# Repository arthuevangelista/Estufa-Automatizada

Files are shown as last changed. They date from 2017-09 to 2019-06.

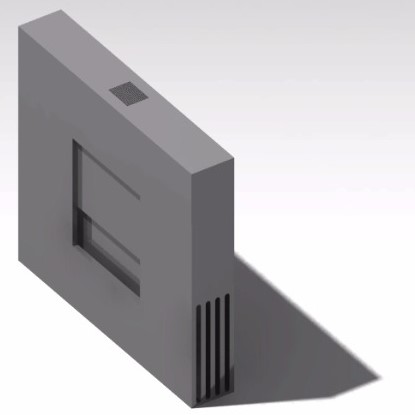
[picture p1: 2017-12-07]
Projeto Final/IMAGENS/WhatsApp Image 2017-11-26.jpeg

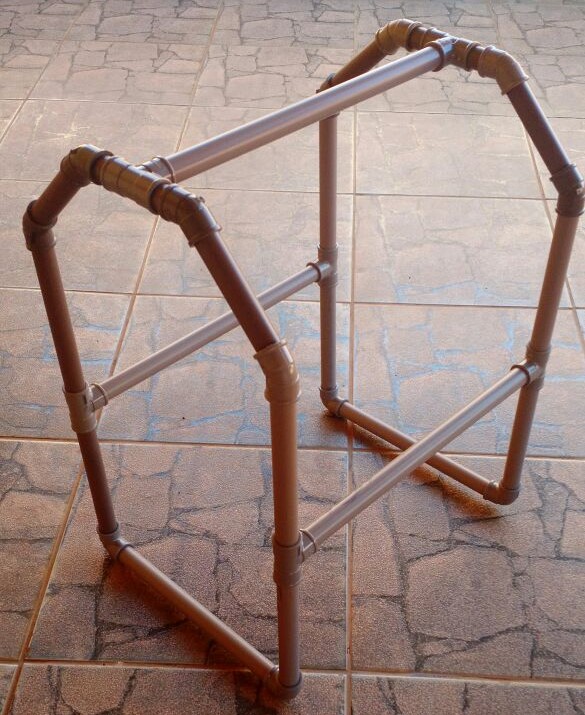
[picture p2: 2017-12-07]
Projeto Final/IMAGENS/WhatsApp Image 2017-11-24.jpeg

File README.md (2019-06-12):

# Estufa Automatizada

Este repositório possui um projeto de estufa automatizada para cultivo de morangos utilizando um microcontrolador MSP430. O projeto nasceu como relatório final da disciplina de Microprocessadores e Microcontroladores ministrada pelos professores Diogo Caetano (em 2017) e Gilmar Bezerra (em 2019) na UnB, campus Gama. As vantagens do uso do MSP430 são o seu baixo custo e seus modos de economia de energia. A proposta é fazer uma pequena cultivar de morangos que seja econômica e conceda as condições ideais de plantio. 

O repositório está organizado da seguinte forma:

- "Código" possui o código em C a ser compilado e carregado no MSP430. É recomendado o uso do software Code Composer Studio. Maiores instruções de instalação, compilação e carregamento podem ser encontradas nesta pasta. O módulo de interfaceamento do sensor DHT11 com o MSP430 foi disponibilizado pelo usuário [_bafeigum_](https://github.com/bafeigum/DHT11-Library-for-MSP430).  
- "Esquemático" possui todos os esquemáticos e diagramas de montagem do projeto. Neste diretório estão inclusos diagramas de PCI (placa de circuito impresso) caso sua produção seja optada. 
- "Relatório" possui alguns relatórios que os autores fizeram em relação ao projeto. Como este projeto nasceu de uma disciplina, esta pasta também possui o relatório final entregue ao professor. Não é recomendado o uso deste relatório por terceiros para fins acadêmicos por constituir plágio.  

Planos futuros para este projeto são a implementação de uma versão em Assembly e um aplicativo de celular ou _webapp_ para monitoramento e controle remoto das condições do plantio.

Autores: [Arthur Evangelista dos Santos](https://github.com/arthuevangelista) e [Guilherme Richard Alves de Oliveira](https://github.com/aogrichard).

O uso e distribuição deste projeto é livre, contanto que sejam identificados seus autores.

===========================================================================================

This repository contains a project of a automated stove for strawberry culture using a MSP430 microcontroller. This project started as a final report for the discipline of Microcontrollers and Microprocessors instructed by the professors Diogo Caetano (in 2017) and Gilmar Bezerra (in 2019) at UnB, Gama campus. The advantages of using the MSP430 are it's relative low cost and it's reduced energy consumption modes. The purpose is making a small strawberry culture that can be economic and provide the ideal plant conditions.

The repository is organized in the following way:

- "Código" has the code in C to be compiled and uploaded for the MSP430. It's recommended that you use Code Composer Studio. Further instructions of installation, compilation and code upload can be viewed in this folder as well. The module for interfacing the sensor DHT11 with MSP430 is provided by the user [_bafeigum_](https://github.com/bafeigum/DHT11-Library-for-MSP430).   
- "Esquemático" has all the schematics and diagrams for the project assembling. In this directory are included the PCB diagrams (printed circuit board) in case you choose to produce one.  
- "Relatório" has some reports that the autors have done in relation to the project. This folder has the final reports for the discline as this project started as a homework. It's not recommended to use those reports by third party with academic purposes as this could be considered plagiarism.  

Future plans for this project are it's implementation with a Assembly Language version and a smartphone app or _webapp_ for remote monitor and control of the plant conditions.

Authors: [Arthur Evangelista dos Santos](https://github.com/arthuevangelista) e [Guilherme Richard Alves de Oliveira](https://github.com/aogrichard).

The use and distribution of this project is free as long as it's authors are identified.

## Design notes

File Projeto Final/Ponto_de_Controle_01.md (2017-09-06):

Micro e Micro - 2.2017

# Ponto de Controle 01

## Projeto de Automação com MSP430

* **Justificativa**
    * O controle hídrico em lavouras, jardins residenciais e estufas tem papel fundamental nas finanças de uma empresa ou residência. Estima-se que boa parte dos gastos com água potável são devido a estas atividades. Em uma situação de crise hídrica como a atual e o preço da água se elevando a cada dia, uma empresa ou residência com controle de seus gastos hídricos obtém vantagem econômica expressiva.

* **Objetivos**
    * Economia de água devido a automação do ambiente;
    * Controle de irrigação do jardim/lavoura/plantação;
    * Captação de dados de umidade e temperatura ambiente;
    * Calcular e fornecer dados estatísticos como temperatura média, umidade relativa, desvios padrões e etc.
      
* **Requisitos**
    * Uso do launchpad MSP430;
    * Uso de uma memória flash externa para armazenamento do banco de dados;
    * Controle do fluxo de água com Relés e válvulas solenóides;
    * Sensores de umidade e temperatura;
    * Módulo Wi-Fi e Bluetooth;
    
* **Benefícios**
    * Uso da opção de low-power mode do MSP430 pode oferecer vantagem nos momentos em que não estiver sendo utilizado;
    * Relés e válvulas todas normalmente fechadas provê economia substancial de energia;
    * Controle hídrico
    
* **Revisão Bibliográfica**
    * 
    
* **Anotações Temporárias**

> Dúvida: Entrada de dados no sistema;

> Banco de dados ficaria armazenado em um dispositivo flash externo ao microcontrolador. Listas encadeadas podem ser uma boa abordagem para guardar elementos, adicionar/remover elementos e etc do banco de dados. **CUIDADO!** Listas são realizadas com alocação dinâmica de memória (pode dar problema na memória RAM do MSP430 se não for especificado que a lista deve estar na memo flash);

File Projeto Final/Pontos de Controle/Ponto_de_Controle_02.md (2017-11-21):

Micro e Micro - 2.2017

# Ponto de Controle 01

## Projeto de Automação com MSP430

* **Módulos utilizados no sistema**
	* Abaixo segue uma lista dos módulos que serão utilizados no sistema até a data de redação deste relatório
	
	* **Level-shifter para redução de tensão**
		* Uma montagem utilizando dois resistores de 10k ohm e um transistor mosfet BS170.
		* O level-shifter reduz a tensão para que seja possível conectar componentes que utilizam diferentes tensões como nível lógico alto. Se um sinal chega com 3,3 V o level-shifter subirá esta tensão para 5 V em sua saída para que seja utilizado por outro componente.
		* A recíproca é verdadeira. Portanto, se um sinal tiver 5 V, a saída do level-shifter terá 3,3 V.
		* Imagem do esquemático do componente abaixo.
		* Testes foram realizados com este componente para verificar se ele funciona e quais os níveis de tensão em sua saída. Houve também uma preocupação quanto à frequência máxima de operação, uma vez que este componente será utilizado na saída de todos os sensores e nas saídas do MSP430. Foi confirmada o nível de ruído apresentado na saída do level-shifter à partir de Hz, de acordo com a informação do datasheet do componente transistor BS170. As imagens abaixo mostram os resultados obtidos nos testes com osciloscópio.

> **LINK PARA DATASHEET DO BS170: https://www.onsemi.com/pub/Collateral/BS170-D.PDF**

   * **Módulo relé 4 canais**
       * Será utilizado um módulo com 4 relés para controle dos dispositivos com tensão de 12V e corrente
    * **Módulo sensor de umidade do solo (umidostato)**

		* Possui formato de garfo (apenas duas pontas que deverão estar fincadas no solo). Ao identificar umidade ocorrerá uma diferença de potencial entre as pontas do garfo. A corrente que passará entre as duas pontas é muito pequena (resistência próxima dos M ohm).

		* Quanto maior a resistência, menor a umidade entre as ponteiras. A corrente, portanto, é muito baixa para que se insira o sensor diretamente na porta analógica do micro. É necesário o uso de um módulo comparador.

			* Nada mais é que um amplificador operacional em modo comparador. Quando comprado o sensor, o comparador LM393 (low offset voltage dual comparator) vem no conjunto.

			* A tensão de trabalho é de 3,3 V a 5 V. O comparador tem quatro pinos: Vcc, GND, D0 (digital) e A0 (analógico). Para usar a saída digital é necessário utilizar o potenciômetro para calibrar o sensor.

			* O potenciômetro irá ajustar em qual medida de umidade a saída digital terá nível lógico zero. OBS.: Podemos utilizar uma entrada digital do MSP430 ativa em alta para identificar quando a umidade está baixa. Ou seja, Quando D0 = 1 -> Umidade baixa. Quando D0 = 0 -> Umidade no solo suficiente, desliga o irrigador.

			* Utilizaremos apenas o pino digital para o projeto. A leitura dos dados de umidade do solo podem ser comutados com a leitura dos dados de umidade do ar (DHT11), liberando a porta digital para outra aplicação.

			* Utilizar uma porta analógica para leitura de dados seria mais preciso, mas exigira um processamento do sinal analógico antes deste ser inserido no microcontrolador (i.e. uma média móvel dos valores para evitar ruído/sinal aleatório).

**REFERÊNCIAS**
> **LINK PARA SENSOR: https://www.filipeflop.com/produto/sensor-de-umidade-do-solo-higrometro/
	LINK PARA O DATASHEET DO LM393: http://www.ti.com/lit/ds/symlink/lm293.pdf**

	* Para visualização dos dados (umidade do ar, umidade do solo e temperatura) será utilizado um display. Dependendo da temperatura será ativado um exaustor (resfriar a estufa) ou uma lâmpada (aquecer a estufa); Da umidade do ar/solo serão ligadas as válvulas de irrigação.

		* Possui uma biblioteca na IDE do arduino #include<LiquidCrystal.h>
		* Pode ser facilmente implementada no MSP430
		* Utilizado para referência do usuário e para verificação dos dados da estufa

	* O sensor DHT11 é responsável por realizar a medição de umidade relativa do ar (usando um sensor do tipo HR202 (entre 20% e 90%)) e da temperatura (usando um termistor NTC (entre 0 e 50 C)). Possui quatro pinos: Vcc, GND, Dados (comunicação UART) e N.C (não utilizada)

		* Possui uma biblioteca própria no Arduino #include<dht.h>

		* Utiliza dois pinos para enviar os dados para o Microcontrolador (ambos analógicos). Para escrever os dados no display, é necessário separar os digitos.

		* É necessário um delay entre uma leitura e a outra (o micro enviará um sinal avisando que está em modo de leitura e o DHT11 enviará outro sinal indicando que está enviando dados). Será utilizada uma interrupção com o timer A para realizar a leitura dos dados.

		* Possui uma biblioteca para msp430 disponível no link do github a seguir: https://github.com/bafeigum/DHT11-Library-for-MSP430

		* Para utilizar esta biblioteca é necessário o uso de um timer e uma interrupção, uma vez que a leitura e escrita exigem um delay entre a comunicação com a placa.
			* Precisa estar setado em UP mode e contando a cada 250 kHz (pode-se utilizar o SMCLOCK sendo /4);
			* ISR seta um volatile unsigned char TOUT no TA0. Esse ISR também deverá dar clear na interrupt flag, setando CCIFG no registrador TACCL0;
			* São enviados 5 elementos de um vetor (chamado packet) para o MSP430:
				* packet[0] = primeiro byte de umidade
				* packet[1] = segundo byte de umidade (deve ser ZERO)
				* packet[2] = primeiro byte de temperatura
				* packet[3] = segundo byte de temperatura (deve ser ZERO)
				* packet[4] = byte da soma dos 4 bytes anteriores (usado para checagem dos dados (em caso de falha na comunicação))

**REFERÊNCIAS**
> **LINK PARA SENSOR: https://www.filipeflop.com/produto/sensor-de-umidade-e-temperatura-dht11/
	LINK PARA O DATASHEET DO DHT11: http://img.filipeflop.com/files/download/Datasheet_DHT11.pdf**

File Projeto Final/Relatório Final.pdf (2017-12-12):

# Estufa Agrícola Automatizada com Auxílio do MSP430 para Cultivo de Morangos

Arthur Evangelista dos Santos Universidade de Brasília, Faculdade do Gama — UnB, FGA Matrícula: 14/0016686
Email: arthuevangelista@hotmail.com

Gabriela Conceiçao dos Santos ˜ Universidade de Brasília, Faculdade do Gama — UnB, FGA Matrícula: 16/0152038
Email: gabrielacsantos.engunb@gmail.com

Abstract—Este projeto visa criar um prototipo de estufa ´ agrícola automatizada para o cultivo de morangos aplicando
sensores eletronicos para controlar as condiç ˆ | oes de umidade e ˜
temperatura com auxílio do microcontrolador MSP430.

Keywords—MSP430, microcontrolador, automaçao, morangos, ˜ estufa.

I. REVISAÕ BIBLIOGRAFICA ´
A. O Morangueiro

O morangueiro pertence a Família Rosaceae. De origem Europeia, as plantas cultivadas para o consumo de sua fruta ´ sao o resultado de um sucessivo trabalho de melhoramento ˜
genetico e cruzamento entre algumas esp ´ | ecies do G ´ | enero ˆ
Fragaria. Atualmente, existem mais de 15 variedades de morangueiros. E um vegetal rasteiro, de caule do tipo estolho, ´ produzindo gemas que permitem com que novas plantas, com raízes e folhas, sejam formadas, assexuadamente. Uma imagem do morangueiro encontra-se abaixo na Fig. 1. No Brasil, sua produçaõ e mais significativa nos meses de junho a dezembro ´
e requer boa umidificaçao do solo. Por este motivo, ˜ | acaros e ´
pulgoes s ˜ | ao suas principais pragas. ˜

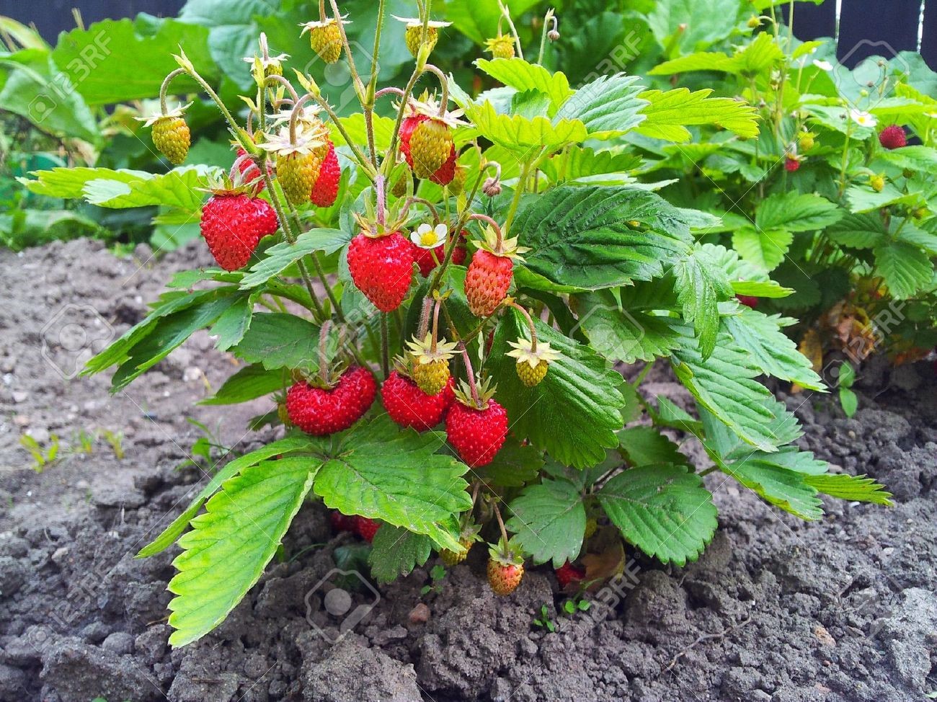
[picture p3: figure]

Fig. 1. Morangueiro

Desta planta origina-se o morango (Fig. 2), cuja parte
vermelha, comestível, e, na verdade, o recept ´ | aculo floral de- ´
senvolvido. Assim, ele e um pseudofruto; sendo os frutos, do ´ tipo aquenio, as estruturas amarronzadas que se encontram ˆ incrustadas nele.

Características gerais do cultivo do morango
:

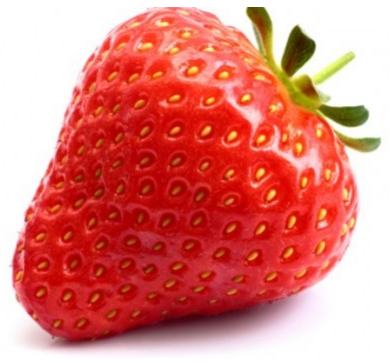
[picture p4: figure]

Fig. 2. Fruto e pseudofruto do morango

- Clima: Locais com temperatura alta durante o dia e baixa durante a noite sao considerados bons para o ˜ cultivo do morangueiro. O calor e importante para o ´ crescimento vegetativo das plantas, enquanto o frio é
imprescindível a frutificaçao. A floraç ˜ | | aõ e favorecida ´
por temperaturas abaixo de 10 ◦C e desfavorecida por temperaturas acima de 25 ◦C. O comprimento do
dia, ou seja, o numero de horas de luz, tamb ´ | | | em tem ´
influencia sobre a produç ˆ | ao. A estas caracter ˜ | ísticas é
dado o nome de fotoperíodo.
Fotoperíodo trata-se da proporçao entre luz e es- ˜ curidao num ciclo de 24 horas (Santos, D.M.M., ˜ 2004). O morango, classificado como planta C3
quanto a fotoss ` | íntese e short-day plant (SDP) quanto
ao fotoperíodo, deve estar exposto por volta de 8 a 10
horas de luz diaria. O per ´ | íodo de escuridao tamb ˜ | em´
possui influencia na produç ˆ | ao de flores. Por ˜ | em, o ´
pouco excesso de iluminaçao devido ˜ | as condiç ` | oes ˜
de solstício ou equinocio na regi ´ | ao n ˜ | ao ter ˜ | a tanta ´
influencia no desenvolvimento do vegetal. Por este
motivo, nao optou-se por um pl ˜ | astico preto ou de ´
coloraçao que evitasse a exposiç ˜ | aõ a iluminaç ` | | ao. ˜
Para manter o fotoperíodo em condiçoes ideias de ˜
plantio, sera utilizada uma interrupç ´ | ao no MSP430 que ˜
ativara um LED capaz de fornecer o espectro de luz ´ apropriado para a planta.
- Sistemas de cultivo: O morango pode ser cultivado em
canteiros a ceu aberto, em estufas e em combinaç ´ | aõ
com o uso de tunel baixo. Atualmente est ´ | | | a sendo ´
implantado o sistema de cultivo hidroponico. ˆ

- Local de plantio: O morangueiro produz melhor em solos areno-argilosos e bem drenados. As areas devem ´
ser de facil acesso e ter bom suprimento de ´ | agua ´
para irrigaçao. Deve ser evitado o plantio em local ˜ recentemente cultivado com tomate, batata, fumo ou
com o proprio morango. H ´ | a de se pesquisar sobre ´
outros metodos que tornem poss ´ | ível o plantio de
culturas morangos no mesmo local. Tambem deve ser ´ evitado o plantio em terras de baixa umida. ´
- Período de plantio: A epoca de plantio varia de acordo ´
com a regiao e a cultivaç ˜ | ao a ser plantada. De um ˜
modo geral, planta-se de janeiro a maio. Em regioes ˜
mais quentes, a epoca recomendada ´ | e de abril a ´
maio. Em locais com altitude acima de 1.000 metros, as cultivares de dia neutro podem ser plantadas até setembro.
- | Irrigaçao: A irrigaç ˜ | ao do morangueiro pode ser feita ˜
por aspersao, por ˜ | em o gotejamento (fertirrigaç ´ | ao) tem ˜
sido mais eficiente e economico. Por este motivo, ˆ
neste trabalho sera utilizado o m ´ | etodo de irrigaç ´ | aõ
por gotejamento. Geralmente irriga-se tres vezes por ˆ semana e com duraçao de 30 a 45 minutos, evitando ˜ o excesso de agua. ´
B. O Morangueiro no Distrito Federal

A cultura do morangueiro iniciou-se no Distrito Federal em meados da decada de 70, tendo sido primeiramente introduzida ´ e conduzida de forma empírica pelos agricultores de origem
japonesa vindos da regiao de Atibaia, S ˜ | ao Paulo, at ˜ | e hoje o ´
principal polo de produç ´ | ao de morango naquele estado. ˜

Estes agricultores pioneiros vieram iniciar o cultivo de hortaliças e de frutas para abastecer o novo mercado do Planalto Central. Muitos foram assentados pelo Instituto
Nacional de Colonizaçao e Reforma Agr ˜ | aria - INCRA, a partir ´
de 1970, no ”Projeto Integrado de Colonizaçao Alexandre ˜
Gusmao (PICAG)”, na Regi ˜ | ao Administrativa de Brazl ˜ | andia, ˆ
atualmente o principal produtor de morango do Distrito Federal.

A cultura do morango adaptou-se muito bem as condiçoes ˜ climaticas e de solo do Planalto Central, que apresenta altitude ´
de aproximadamente 1000 metros. Alem disso, essa regi ´ | aõ
possui temperaturas mais altas no verao, que favorecem a ˜
produçao de mudas e na sequ ˜ | encia passa por um inverno ˆ
ameno e seco, o que auxilia no período de floraçao, frutificaç ˜ | aõ
e melhora de forma significativa a qualidade dos frutos cultivados.
Segundo a Emater-DF (Empresa de Assistencia T ˆ | ecnica ´
e Extensao Rural do Distrito Federal), no ano de 2016, a ˜ safra de morangos no Distrito Federal alcançou cerca de 5250 toneladas, numeros que colocam o Distrito Federal na disputa ´ do sexto lugar da produçao nacional entre os estados produ- ˜
tores da fruta . Sao, em m ˜ | edia, 240 produtores de morango ´
em todo o DF. Desses, 35% de produtores agrícolas da cidade sao os que distribuem o que se consome no DF. ˜
C. Estufas Agrícolas

Em grande parte da historia da humanidade, fomos ´ caçadores-coletores. Ha cerca de 10.000 anos, começamos a ´ domesticar plantas e animais como uma forma de tornar a nossa oferta de alimentos mais acessível e previsível.

Sendo assim, para melhorar a produçao agr ˜ ícola, surgiram as estufas agrícolas. O objetivo do cultivo agrícola em estufas
e proporcionar um ambiente controlado, em relaç ´ | ao a fatores ˜
climaticos como temperatura, umidade, luz e quantidade de ´ agua (rega), para que as plantas possam ter um crescimento ´ em um ambiente ideal (Silva, 1976).

A estrutura de uma estufa agrícola depende bastante de
sua finalidade. Geralmente, e constitu ´ | ída por uma armaçao, ˜
de alumínio ou outro material resistente, com uma altura suficiente para poder cultivar e caminhar dentro sem incomodos, ˆ
ela e coberta por um pl ´ | astico transparente, em alguns casos ´
possui uma tela, conhecida como sombrite, que auxilia na regulagem da temperatura interna da estufa alem de ventiladores ´ e em alguns casos lampadas para o controle de luminosidade ˆ (Fig. 3).

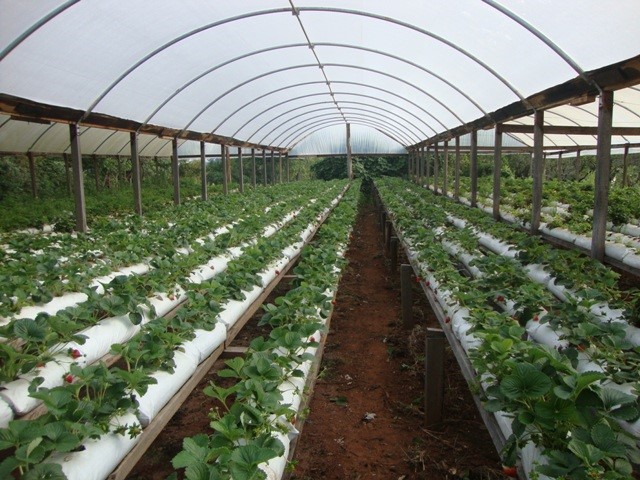
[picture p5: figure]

Fig. 3. Estrutura de uma estufa convencional para o cultivo de morangos

O aumento significativo da utilizaçao de estufas se deu, ˜
em parte, pela criaçao do pl ˜ | astico, devido ao seu baixo custo e ´
versatilidade, porem existem outros fatores que influenciam tal ´ fato, como o melhor desenvolvimento do plantio, aumento de produtividade, colheita nas entressafras e produtos de melhor qualidade.
D. Automaçao de Estufas ˜

Em uma estufa existem diversas variaveis que podem ser ´ monitoradas e verificadas para o controle do plantio, como temperatura, umidade e luminosidade. Considerando o ponto de vista dos produtores agrícolas, a correta leitura dos dados e posterior tomada de decisao pode trazer resultados satis- ˜ fatorios. ´

A automatizaço de uma estufa ˜ | e uma excelente ferramenta ´
de auxílio ao agricultor, pois permite a tomada de deciso no ˜
momento certo, conforme a analise das vari ´ | aveis verificadas. ´

II. JUSTIFICATIVA

Apesar de ser considerado um dos maiores produtores de morango do Brasil, durante o de 2017, o Distrito Federal veio enfrentando um grave crise hídrica, o que afetou de

forma significativa a produçao de morangos nessa regi ˜ | ao. ˜
Segundo dados da Emater, a restriçao no abastecimento de ˜
agua provocou a diminuiç ´ | ao da ˜ | area plantada em cerca de ´
30%, de 150 hectares em 2016 para 105 hectares neste ano.
Alem disso, a desaceleraç ´ | ao na produç ˜ | ao de mercado de ˜
morangos do DF ocasionou a diminuiçao do n ˜ | umero de tra- ´
balhadores envolvidos direta e indiretamente com a atividade, gerando a queda na renda das famílias e do Produto Interno Bruto(PIB) do Morango.

Diante disso, a escolha do projeto de construçao de uma ˜ estufa automatizada foi motivada pela simples possibilidade de se oferecer uma nova alternativa para o melhoramento do cultivo de morangos no Distrito Federal , uma vez que a estufa proposta sera capaz de controlar todas as necessi- ´ dades da cultura e o ambiente da estufa, o que proporcionará aos produtores mais qualidade em seus frutos e uma maior
renda. Tambem ser ´ | a poss ´ | ível controlar a quantidade de agua ´
utilizada na irrigaçao da plantaç ˜ | ao gerando, consequentemente, ˜
economia de recursos hídricos e financeiros na produçao de ˜ morangos.

III. OBJETIVOS

Considerando que cada especie de planta necessita de ´
situaçoes clim ˜ | aticas diferentes e espec ´ | íficas para se desen-
volver, o projeto proposto tem o intuito de otimizar o cultivo de morangos atraves do desenvolvimento de uma estufa capaz de ´ gerenciar (monitorar e atuar) o controle das condiçoes ambien- ˜
tais dentro do ambiente da estufa atraves da disponibilizaç ´ | aõ
de recursos de automaçao como irrigaç ˜ | ao autom ˜ | atica, sistemas ´
de ventilaçao, iluminaç ˜ | ao e controle de temperatura ambiente, ˜
utilizando o microcontrolador MSP430.

Em resumo, os objetivos deste trabalho sao: ˜

- | Economia de agua devido a automaç ´ | ao do ambiente; ˜
- Captaçao de dados de umidade e temperatura ambi- ˜ ente;
- Captaçao de dados de umidade do solo; ˜
- Controle de irrigaçao da estufa; ˜
- | Controle da iluminaçao e do fotoper ˜ | íodo da planta;
- Controle da temperatura no ambiente interno da estufa;
- Apresentaçao dos dados adquiridos pelos sensores ao ˜ usuario. ´

IV. REQUISITOS
- Uso do launchpad MSP430;
- | Controle do fluxo de agua com Rel ´ | es e v ´ | alvulas ´
| solenoides; ´
- Sensores de umidade e temperatura;
- Display para apresentaçao dos dados; ˜
- Fontes para fornecimento de 3.3 V, 5 V e 12 V para
| o sistema;
- LED capaz de fornecer o espectro de luz necessario ´
| para planta;
- | Pastilha termica para o r ´ | apido ajuste de temperatura; ´
V. BENEFÍCIOS
- | Uso da opçaõ | low-power mode do MSP430 pode
oferecer vantagem nos momentos em que nao estiver ˜ sendo utilizado;
- | Os reles e v ´ | alvulas todas e modo normalmente fechado ´
(NC) prove economia substancial de energia; ˆ
- Controle do consumo de recursos hídricos;
- Monitoramento do crescimento da planta e dos relacionados ao microclima no qual ela se encontra;
- Certeza de colheita no período de safra e entressafra;
- Economia de tempo e dinheiro para o produtor com o trabalho relacionado ao plantio e colheita dos morangos.

VI. ESTRUTURA

A estrutura do prototipo da estufa foi inicialmente cons- ´ truída com canos PVC (Policloreto de Vinila) de 25 mm de
diametro, e coberta com filme pl ˆ | astico transparente. A escolha ´
desses materiais foi feita pois se tratam de materiais resistentes, acessíveis, de baixo custo e suprem bem as necessidades de controle do mini-ecossistema da estufa. Como mencionado
tambem na seç ´ | ao I-A, n ˜ | ao optou-se por um pl ˜ | astico preto ou ´
de coloraçao que evitasse a exposiç ˜ | aõ a iluminaç ` | ao. ˜

As dimensoes da estruturas foram determinadas a partir da ˜ densidade de plantio estipulada para o cultivo do morangueiro em estufas, onde esta define que o espaçamento entre os morangueiros deve ser de no mínimo 20 cm e altura maxima ´ que a planta pode atingir 30 cm.

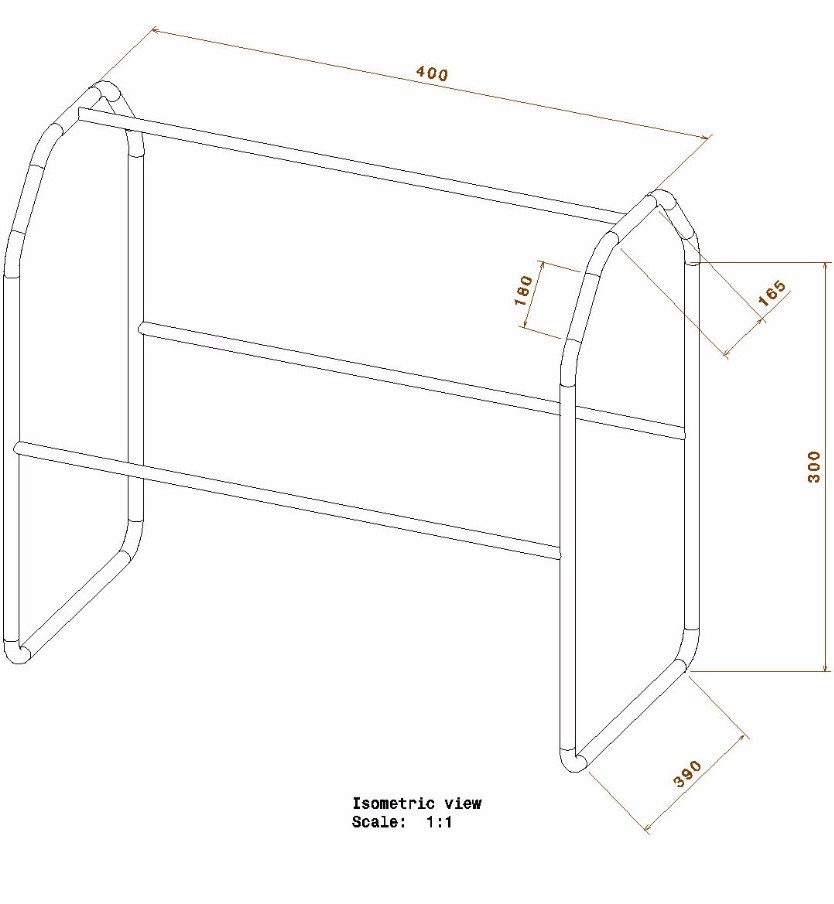
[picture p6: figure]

Fig. 4. Vista Isometrica do CAD da Estrutura realizado no software CATIA. ´


Fig. 5. Estrutura construída em cano PVC.

VII. COMPARTIMENTO PARA ELETRONICA ˆ

Tendo em vista a acomodaçao dos componentes ˜ eletronicos, optou-se por montar uma segunda estrutura ˆ para concentrar tais componentes. Trata-se de uma caixa de
madeira MDF onde serao concentrados: o MSP430, o m ˜ | odulo ´
level-shifter, o display de cristal líquido, a pastilha termica e ´
os coolers, as fontes de alimentaçao e o m ˜ | odulo rel ´ | e. Assim, ´
a realizaçao da manutenç ˜ | ao em algum destes componentes ˜
torna-se de facil acesso. Outra vantagem ´ | e a facilidade de ´
acesso quanto a etapa de testes nos componentes e validaçaõ de algoritmos no MSP430. Os demais componentes (os sensores DHT11, umidostato e o LED de espectro completo) devem interagir diretamente com o ambiente interno a estufa `
e, portanto, estao no interior do pl ˜ | astico transparente de ´
cobertura da estufa.
Esta caixa contara com aberturas para circulaç ´ | ao de ar na ˜
regiao inferior e na superior, como pode ser observado nas ˜ Fig. 6 e no detalhamento na Fig. 7. A motivaçao para esta ˜
configuraçao se d ˜ | a pela exaust ´ | ao do cooler de resfriamento ˜
da pastilha termica estar contida neste compartimento. A ´ configuraçao das aberturas inferiores favorece o estrangula- ˜ mento do fluxo de ar, aumentando sua velocidade e fazendo com que o ar frio e menos denso resfrie os componentes do compartimento interno. As aberturas superiores tambem´ estrangulam o fluxo de ar, fazendo com que o ar quente e interno do compartimento saia com maior velocidade para o ambiente externo.
Maiores detalhes quanto a configuraç ` | ao dos coolers e ˜
o funcionamento da pastilha termica estar ´ | ao na seç ˜ | ao VIII. ˜
Resumidamente, a pastilha e um paralelep ´ | ípedo com pouca
espessura. Esta aquecera de um lado e resfriar ´ | a do outro ´
e as aletas de alumínio em conjunto com os coolers seraõ responsaveis pela troca de calor externo. Como ambos os lados ´ poderao aquecer ou resfriar, foram colocadas aletas e coolers ˜ nos dois lados. Este conjunto esta apoiado no compartimento ´
para eletronica e um dos lados estar ˆ | a virado para o interior da ´
estufa.

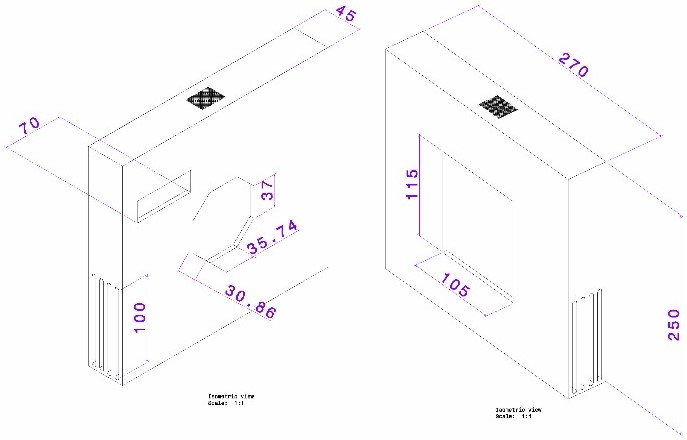
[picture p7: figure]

Fig. 6. Vista Isometrica do CAD do compartimento para eletr ´ | onica realizado ˆ
no software CATIA.

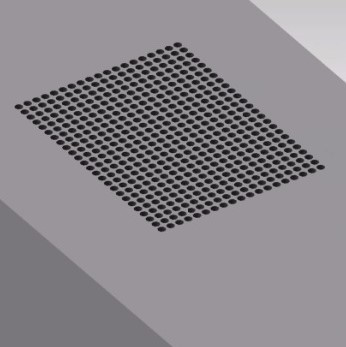
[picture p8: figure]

Fig. 7. Detalhamento da abertura superior do compartimento para eletronica. ˆ

VIII. VISAÕ GERAL DO SISTEMA

O sistema do projeto proposto pode ser dividido duas partes. Uma parte de hardware, dotado do microcontrolador
MSP430, sensores eletronicos, os quais s ˆ | ao encarregados pela ˜
aquisiçao de dados do sistema, e atuadores, respons ˜ | aveis por ´
irrigar, iluminar, ventilar e reduzir ou aumentar a temperatura. E uma parte de software, responsavel pelo processamento dos ´ dados e do controle dos perifericos atuadores. ´

A. Hardware
1) Lista de Componentes:
- MSP-EXP430G2553LP;
- Sensor de luz (LDR 5mm);
- Sensor de temperatura e umidade (DHT11);
- Resistores de 10kOhm;
- Transistor Mosfet BS170;
- Modulo sensor de umidade do solo (Umidostato); ´
- | Modulo rel ´ | e 4 canais; ´
- LED de espectro completo;
- Pastilha termina de efeito Peltier TEC1-12706; ´
- 2 Coolers de 12V;
- Fontes de 3,3V, 5V e 12V;
- | Valvula Solen ´ | oide. ´
2) Descriçao do Hardware: ˜ | Para melhor ilustrar a mon-
tagem dos componentes, foi realizado um diagrama de blocos para o sistema, que pode ser visualizado na Fig. 8. Uma breve
descriçao de cada componente ser ˜ | a apresentada a seguir. ´

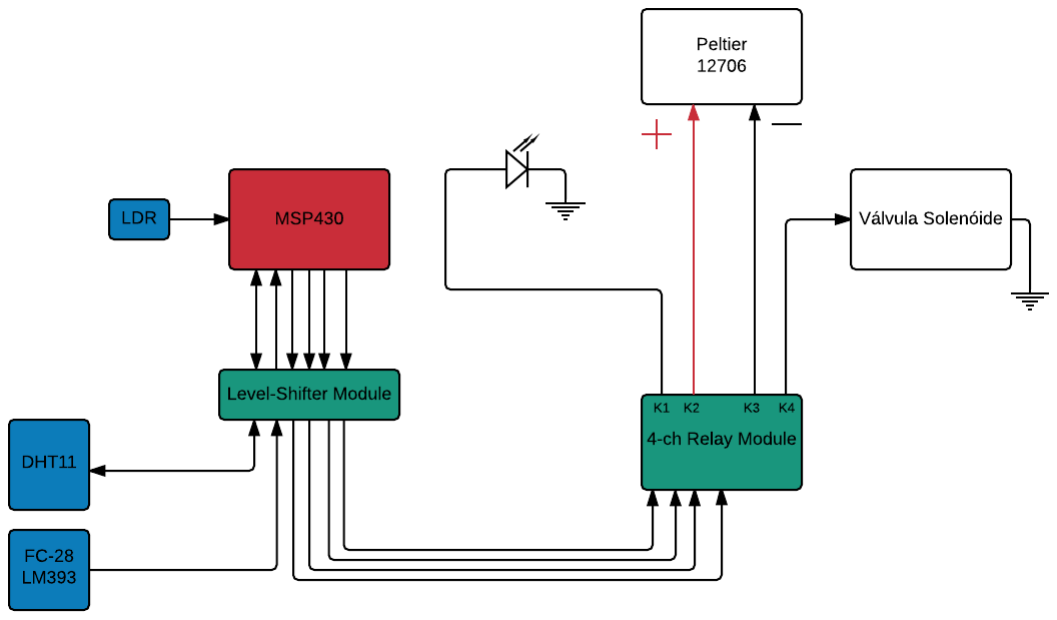
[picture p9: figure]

Fig. 8. Diagrama de Blocos do sistema da estufa.

- MSP-EXP430G2553LP: O MSP430 sera o micro- ´ controlador responsavel pelo processamento dos dados ´ e a tomada de decisao de acordo com os dados. ˜ Este componente recebera os dados de temperatura e ´ umidade relativa do ar no interior da estufa, os dados de umidade do solo e os dados de luminosidade e
tomara as decis ´ | oes melhor descritas na seç ˜ | ao VIII-A3. ˜
- Sensor de luz (LDR 5mm): Apos consultoria a ´
colegas da area de fisiologia vegetal e devido ´ | as`
características fotoperiodicas do morango, foi optado ´ pelo uso de um sensor de luminosidade LDR (Light Dependent Resistor) para identificar a existencia ou ˆ
nao de luminosidade na regi ˜ | ao pr ˜ | oxima ´ | a planta. O `
sensor e basicamente um resistor que ao submetido ´ | à
luz, aumenta sua condutividade eletrica. ´
- | Level-shifter para reduçao de tens ˜ | ao: ˜ | Uma mon-
tagem utilizando dois resistores de 10k ohm e um transistor mosfet BS170. O level-shifter reduz a tensaõ para que seja possível conectar componentes que
utilizam diferentes tensoes como n ˜ | ível logico alto. Se ´
um sinal chega com 3,3 V o level-shifter subira esta ´
tensao para 5 V em sua sa ˜ | ída para que seja utilizado
por outro componente.
A recíproca e verdadeira. Portanto, se um sinal tiver ´ 5 V, a saída do level-shifter tera 3,3 V. Testes foram ´ realizados com este componente para verificar se ele
funciona e quais os níveis de tensao em sua sa ˜ | ída.
Houve tambem uma preocupaç ´ | ao quanto a frequ ˜ | encia ˆ
maxima de operaç ´ | ao, uma vez que este componente ˜
sera utilizado na sa ´ | ída de todos os sensores e nas
saídas do MSP430. Foi confirmada o nível de ruído apresentado na saída do level-shifter a partir de 5MHz, o que ratifica a informaçao fornecida pelo ˜ datasheet do componente transistor BS170.
O esquematico desta montagem encontra-se na Fig. 9 ´ abaixo.

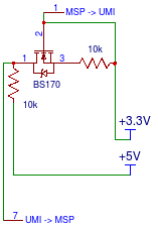
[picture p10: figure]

Fig. 9. Esquematico da unidade ´ | level-shifter (redutora de tensao). ˜
Tambem foi realizada um esquem ´ | atico para todos ´
redutores de tensao que ser ˜ | ao utilizados no projeto e ˜
foi montada um layout para placa de circuito impresso (PCB do inglesˆ printed circuit board). O intuito de se utilizar uma PCB e facilitar a montagem do circuito e ´
evitar perdas de tensao, diminuindo o ru ˜ | ído devido as`
linhas de transmissao do sinal. At ˜ | e a data de redaç ´ | aõ
deste relatorio, a PCB encontra-se em sua vers ´ | ao 1.0. ˜
O estudo quanto ao uso de ground plate para reduçaõ
de ruído esta em andamento para as demais vers ´ | oes. ˜
- | Modulo rel ´ | e 4 canais: ´ | Sera utilizado um m ´ | odulo ´
com 4 reles para controle dos dispositivos com tens ´ | aõ
de 12V (pastilha termica e a v ´ | avula solen ´ | oide) e do ´
LED de espectro completo de 3,3V que consume uma corrente acima da suportada pelo MSP430

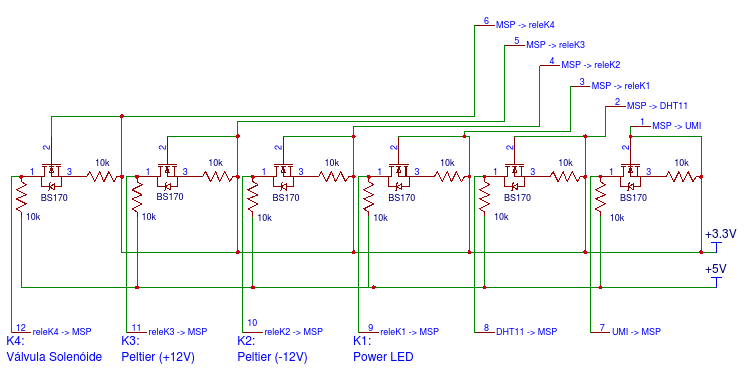
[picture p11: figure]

Fig. 10. Esquematico do bloco de ´ | level-shifter’s utilizados no projeto.

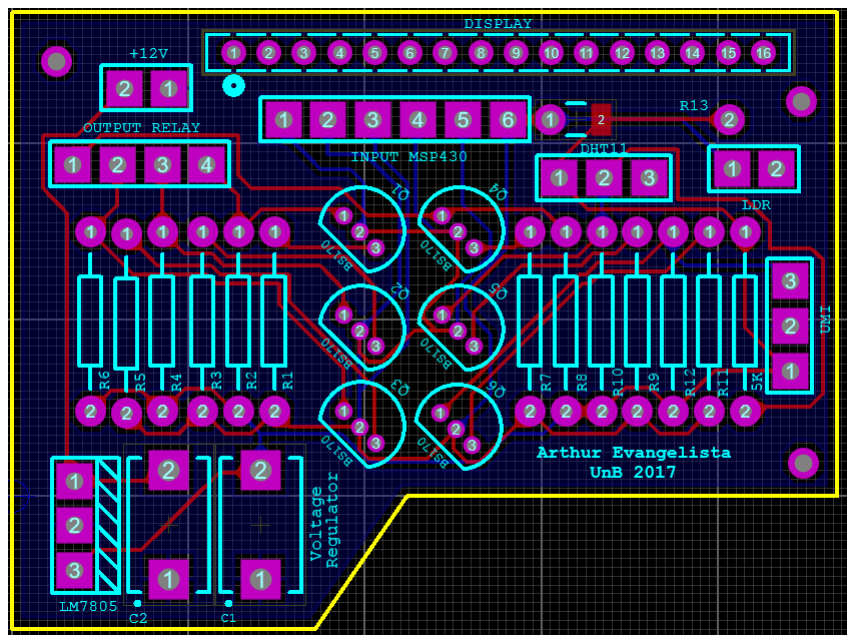
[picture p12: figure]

Fig. 11. Layout para PCB a ser confeccionada para o projeto.

- Modulo sensor de umidade do solo (umidostato): ´ Possui formato de garfo (apenas duas pontas que deverao estar fincadas no solo). Ao identificar umidade ˜ ocorrera uma diferença de potencial entre as pontas do ´
garfo. A corrente que passara entre as duas pontas ´ | é
muito pequena (resistencia pr ˆ | oxima dos M ohm). ´
Quanto maior a resistencia, menor a umidade entre as ˆ ponteiras. A corrente, portanto, e muito baixa para que ´ se insira o sensor diretamente na porta analogica do ´
micro. E necess ´ | ario o uso de um m ´ | odulo comparador. ´
Nada mais e que um amplificador operacional em ´ modo comparador. Quando comprado o sensor, o comparador LM393 (low offset voltage dual comparator) vem no conjunto.
A tensao de trabalho ˜ | e de 3,3 V a 5 V. O comparador ´
tem quatro pinos: Vcc, GND, D0 (digital) e A0
(analogico). Para usar a sa ´ | ída digital foi necessario ´
utilizar o potenciometro j ˆ | a encontrado no m ´ | odulo para ´
calibrar o sensor.
O potenciometro ir ˆ | a ajustar em qual medida de umi- ´
dade a saída digital tera n ´ ível logico zero. Podemos ´ utilizar uma entrada digital do MSP430 ativa em alta para identificar quando a umidade esta baixa. Ou seja, ´ Quando D0 = 1 a umidade esta baixa. Quando D0 = ´
0, ha umidade suficiente, n ´ | ao h ˜ | a necessidade de ligar ´
o irrigador (valvula solen ´ | oide). ´
Utilizaremos apenas o pino digital para o projeto. A leitura dos dados de umidade do solo podem ser comutados com a leitura dos dados de umidade do ar (DHT11), liberando a porta digital para outra aplicaçao. ˜
Utilizar uma porta analogica para leitura de dados ´ seria mais preciso, mas exigira um processamento do ´ sinal analogico antes deste ser inserido no microcon- ´ trolador (tecnicas de amostragem do sinal, uso do ´
criterio de Nyquist e o uso de uma m ´ | edia m ´ | ovel ou ´
filtro digital para evitar ruído ou sinais aleatorios ´ | ).
- Display de Cristal Líquido: Para visualizaço dos ˜ dados (umidade do ar, umidade do solo e temperatura) sera utilizado um display. Dependendo da temperatura ´ sera ativado um exaustor (ventilar a estufa) e uma ´ pastilha termica (aquece ou resfria o ambiente da est- ´
ufa). Da umidade do ar/solo serao ligadas as v ˜ | alvulas ´
de irrigaçao. ˜
Possui uma biblioteca na IDE do arduino: (#include¡LiquidCrystal.h¿) e pode ser facilmente implementada no MSP430 utilizando algoritmos disponíveis na documentaçao do fabricante. O display ˜
sera meramente utilizado para refer ´ | encia do usu ˆ | ario ´
quanto aos dados do mini-clima da estufa.
- | Sensor DHT11: O sensor DHT11 e respons ´ | avel por ´
realizar a mediçao de umidade relativa do ar (usando ˜ um sensor do tipo HR202 (entre 20% e 90%)) e da temperatura (usando um termistor NTC (entre 0 e 50 ◦C)). Possui quatro pinos: Vcc, GND, Dados (comunicaçao UART) e N.C (pino vazio). Possui uma ˜ biblioteca propria no Arduino #include¡dht.h¿. ´
Para escrever os dados no display, e necess ´ | ario separar ´
os dígitos. Por se tratar de um sensor de comunicaçaõ
UART, e necess ´ | ario um delay entre uma leitura e a ´
outra. O MSP430 enviara um sinal para o ´ | slave (o
sensor) avisando que esta em modo de leitura e o ´
DHT11 enviara outro sinal para o ´ | master (o MSP430)
indicando que esta enviando dados. Ser ´ | a utilizada uma ´
interrupçao com o timer A para realizar o delay de ˜ leitura dos dados.
Possui uma biblioteca para MSP430 disponível no link do github a seguir: https://github.com/bafeigum/DHT11-Library-for-MSP430.
O princípio de funcionamento desta biblioteca é semelhante ao descrito anteriormente. E utilizado um ´
timer (o timer A) e uma interrupçao para comunicaç ˜ | aõ
com a placa:
- Precisa estar setado em UP mode e contando a cada 250 kHz (pode-se utilizar o SMCLOCK sendo /4);
- ISR seta um volatile unsigned char TOUT no
TA0. Esse ISR tambem dever ´ | a dar clear na ´
interrupt flag, setando CCIFG no registrador TACCL0;
- Sao enviados 5 elementos de um vetor ˜ (chamado packet) para o MSP430: packet[0] = primeiro byte de umidade packet[1] = segundo byte de umidade (deve ser ZERO)
packet[2] = primeiro byte de temperatura packet[3] = segundo byte de temperatura (deve ser ZERO)

packet[4] = byte da soma dos 4 bytes anteriores (usado para checagem dos dados (em caso de falha na comunicaçao)) ˜

- | Valvula Solen ´ | oide: ´ | Basicamente uma chave de
| pressao. Quando passa corrente pelos seus terminais ˜
ele libera a passagem do fluxo de agua. Caso contr ´ | ario, ´
a valvula se mant ´ | em em estado normalmente fechado ´
| e nao consome energia. ˜
- LED de Espectro Completo: O LED de espectro completo utilizado pode ser visualizado na Fig. 12 abaixo. Este LED utiliza uma alimentaçao de 3,3V ˜ e consome por volta de 0,9 A de corrente, fornecendo quase 3W de potencia luminosa para o sistema. De ˆ
acordo com o grafico da Fig. 13, dispon ´ | ível no
datasheet do componente, o espectro de luz que este
| LED fornece e o suficiente para manter a fotoss ´ | | íntese
da planta no trecho de claridade de seu fotoperíodo. Para controlar este LED, sera utilizado o canal K1 do ´
| rele, ligado a uma das sa ´ | | ídas do MSP430. A escolha
para esta configuraçao se deve ˜ | a corrente consumida `
pelo LED que e muito superior ´ | a maior corrente `
fornecida pelo MSP430. Outra vantagem de se utilizar
| o modulo rel ´ | é e a proteç ´ | ao contra fugas de corrente ˜
| do rele para o dispositivo que o controla. ´

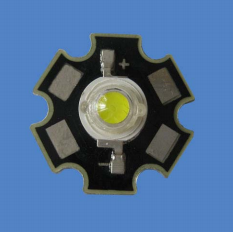
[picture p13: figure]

Fig. 12. LED de espectro completo e da PCB de alumínio do conjunto.

- Pastilha Termica de Efeito Peltier TEC1-12706: ´
Sera utilizada uma pastilha t ´ | ermica de efeito Peltier ´
(TEC1-12706) em conjunto com os Coolers de 12V para o aquecimento e resfriamento da estufa. Esta pastilha necessita de uma fonte de alimentaçao de ˜ 12V e consome ate 6A para manter o efeito em ´ sua superfície. O efeito Peltier ocorre quando dois materiais, quando aplicada uma corrente, em uma junçao do material dissipar calor e na outra absorver ˜ calor. A energia dissipada ou absorvida e proporcional ´ a corrente eletrica (Bobean, 2013). ´
A pastilha TEC1-12706 (Fig. 14) utilizada neste pro-
jeto prove resfriamento de at ˆ | e -30 ´

◦C de uma lado
e aquecimento de ate +70 ´ | ◦C do outro. Para evitar a
queima do componente, transferir o calor do ambiente para a pastilha e vice-versa, e aumentar a area de fluxo ´

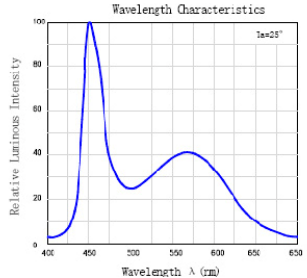
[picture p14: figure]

Fig. 13. Grafico da caracter ´ | ística optica do LED de espectro completo ( ´ | fonte:
3W High Power LED datasheet).
termico, foram instaladas aletas de alum ´ | | ínio. As aletas
transferem o calor do e para o ambiente pelo fenomeno ˆ de conduçao t ˜ ermica. ´

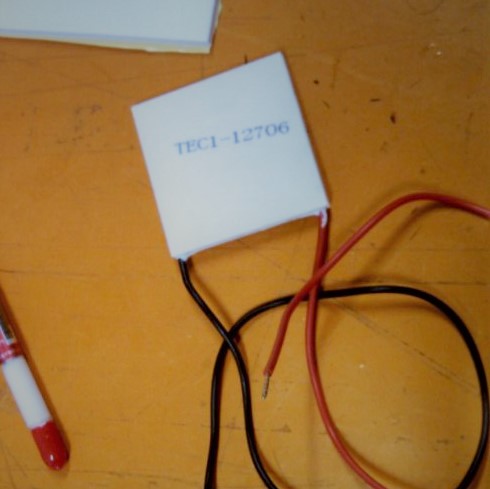
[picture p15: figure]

Fig. 14. Pastilha Termica de Efeito Peltier TEC1-12706. ´

Como citado brevemente na seçao VII, ambos os ˜ lados da pastilha poderao aquecer ou resfriar, a de- ˜ pender da polaridade da tensao submetida. Portanto, ˜ foram colocadas aletas e coolers nos dois lados da pastilha. O conjunto esta apoiado no compartimento ´
para eletronica e um dos lados estar ˆ | a virado para o ´
interior da estufa.
Testes foram realizados com o conjunto montado para certificar seu funcionamento. Quando invertida a polaridade da tensao pelos canais K2 e K3 do ˜

modulo rel ´ | e, a pastilha rapidamente aquece ou resfria. ´
A Fig. 15 a seguir melhor ilustra o funcionamento deste conjunto.

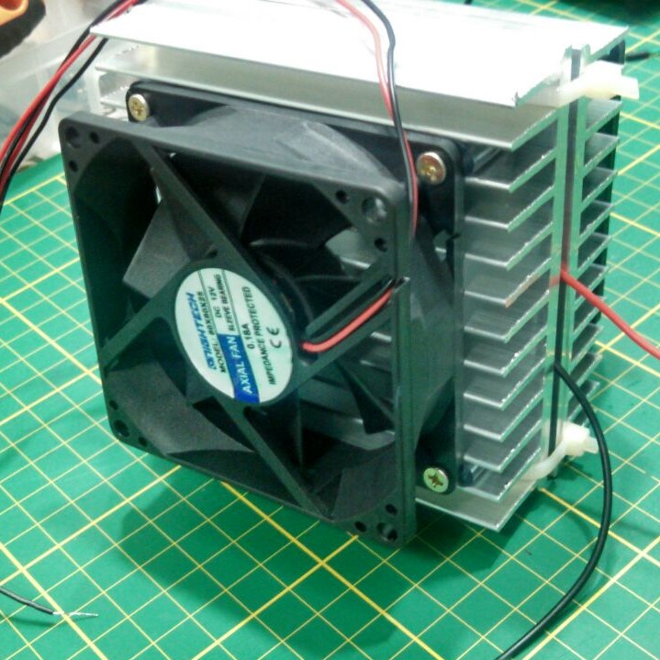
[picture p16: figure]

Fig. 15. Conjunto do sistema de aquecimento/resfriamento montado.

- Coolers 12V: Serao utilizados dois Coolers de 12V ˜ para realizar o transito de ar no ambiente interno à estufa e no ambiente externo. Para o ambiente interno,
o Cooler (Cooler A) ira puxar o ar e lançar ´ | a este fluxo ´
com maior velocidade nas aletas. Quando em contato
com estas aletas, ocorrera o fen ´ | omeno de conduç ˆ | aõ
termica que resfriar ´ | a ou aquecer ´ | a o ar, posteriormente ´
lançado nas aberturas da estrutura de alumínio.
Para o ambiente externo, o Cooler (Cooler B) irá
executar o mesmo procedimento, porem o intuito ´ | é
a troca de ar com o ambiente externo para evitar que o material semicondutor da pastilha superaqueça. De acordo com leitura realizada do livro de Swart (2008), o caso de superaquecimento resultara em uma maior ´
agitaçao dos ˜ | atomos do semicondutor fazendo com ´
que o semicondutor passe da banda de transiçao para ˜
banda de conduçao. Neste caso, a pastilha se tornar ˜ | á
um curto-circuito e podera danificar o projeto. ´
A configuraçao do Cooler A e Cooler B foram plane- ˜ jadas de modo que nao ocorram casos de superaquec- ˜ imento como o mencionado anteriormente e permitam a circulaçao e troca de calor com os ambientes interno ˜ e externo a estufa. `
- | Fontes de tensao 5V e 12V: ˜ | Para alimentaçao do ˜
sistema e de seus componentes, serao utilizadas 2 ˜ fontes de alimentaçao. Uma fonte de 5V para ali- ˜ mentar os sensores, o MSP430, o LED de espectro completo e o modulo level-shifter que necessitam de ´
5V de alimentaçao. ˜ | E poss ´ | ível a alimentaçao de 5V ˜
no MSP430 pois a launchpad fornecida pela Texas Instruments (TI) ja vem equipada com circuito redutor ´
de tensao. Um redutor de tens ˜ | ao montado com uma ˜
configuraçao de resistores ser ˜ | a utilizado para alimentar ´
o LED de espectro completo. Todos estes componentes consumirao, no caso mais pessimista, um total ˜ de 0,86 A.
A segunda fonte de alimentaçao ser ˜ a utilizada para ´ alimentaçao dos componentes que exigem 12V. Estes ˜
sao os Coolers A e B, a pastilha t ˜ | ermica TEC1-12706 ´
e a valvula solen ´ | oide. Estes componentes consumir ´ | ao, ˜
no caso mais pessimista, um total de 6,94 A. O alto
consumo de energia se deve a pastilha t ` | ermica. Vale ´
ressaltar que esta pastilha nao estar ˜ | a funcionando a ´
todo momento.
Pode ser utilizada apenas uma fonte de 12V, regulando sua tensao para 5V para os demais componentes. O ˜ regulador de tensao para 5V consiste em um circuito ˜ utilizando o LM7805 e dois capacitores. A serie ´
LM78XX e composta por reguladores de tens ´ | ao cuja ˜
entrada e 12V e a sa ´ | ída e XX, a depender do valor ´
do regulador. Sendo assim, o regulador LM7805 tem em sua saída 5V, LM7809 tem em sua saída 9V e
assim por diante. Este estara incluso na vers ´ | ao 3.0 da ˜
placa de circuito impresso. Para ligar o LED de 3,3V
e necess ´ | ario o uso de um resistor de 1,8 ohm com ´
capacidade de suportar 3W ou um potenciometro. ˆ
3) Descriçao do Software: ˜ | Para melhor ilustrar o caminho
logico deste sistema, foi constru ´ | ído um Diagrama Logico que ´
encontra-se na primeira pagina de anexos deste trabalho. O ´
codigo do MSP430 dever ´ | a executar os seguintes passos: ´
- Realizar a leitura dos dados de temperatura e umidade relativa do ar adquiridos pelo sensor DHT11 e recebidos via comunicaçao UART (como descrito na ˜ seçao VIII-A2). ˜
- Realizar a leitura dos dados de umidade do solo adquiridos pelo sensor FC-28 e pelo comparador LM393 recebidos via porta de entrada digital. Caso o
sensor apresente resultado nível logico um, h ´ | a pouca ´
umidade. Caso o sensor apresente nível logico zero, ´ ha umidade suficiente. A calibragem do sensor foi ´ realizada conforme descrito na seçao VIII-A2. ˜
- Realizar a leitura dos dados de luminosidade adquiridos pelo sensor LDR de 5mm. Esta entrada ate o ´
momento da redaçao deste relat ˜ | orio est ´ | a como entrada ´
analogica. Quando esta entrada apresentar resultado ´
zero, significa que nao h ˜ | a luminosidade na regi ´ | aõ
proxima ´ | a planta. `
- | Quanto a estrutura de decis ` | ao do MSP430: ˜
- Se a temperatura nao for ideal para o desenvolvimento, ˜ devera ser realizado um ajuste. Para este ajuste, os ´
canais de entrada K2 e K3 do modulo rel ´ | e estar ´ | aõ
conectadas a duas portas de saída do MSP430.
Se a temperatura for abaixo de um certo threeshold, as saídas conectadas nos canais deverao ser K2 = 0 e ˜ K3 = 1, respectivamente. Este comando ira polarizar ´
um dos lados da pastilha termica, o que resultar ´ | a no ´
aquecimento da estufa.
Se a temperatura for acima deste threeshold, as saídas deverao resultar em K2 = 1 e K3 = 0. Deste modo, ˜
a polarizaçao da pastilha t ˜ | ermica ser ´ | a inversa e, por- ´
tanto, ocorrera o resfriamento da estufa. ´
Se a temperatura estiver no patamar ideal, K2 = 0 e K3
= 0, o que cortara a alimentaç ´ | ao da pastilha t ˜ | ermica. ´
- Se o solo nao estiver com a quantidade ideal de ˜
umidade sera ligado o canal K4 do m ´ | odulo rel ´ | e,´

conectado a uma saída do MSP430, e sera iniciada ´ uma contagem. A referida sub-rotina de ativaçaõ do canal K4 e a contagem estarao na linguagem ˜ Assembly do microcontrolador, utilizando a funçaõ

asm()paraexecuçaodesub ˜ | −rotinasassemblyinline.
Esta contagem sera previamente calibrada para que a ´
valvula solen ´ | oide, ativada pelo canal K4, libere apenas ´
a quantidade ideal de agua para o solo, evitando que ´ a planta fique encharcada. Para esta contagem, será utilizada a contagem de ciclos de clock para cada instruçao de desvio em Assembly. ˜
- | Se nao houver luminosidade que seja ˜ | util ao desen- ´
volvimento da planta, sera tomado em consideraç ´ | aõ
a relaçao fotoperi ˜ | odica da planta. ´ | Fotoperíodo trata-
se da proporçao entre luz e escurid ˜ | ao num ciclo de ˜
24 horas (Santos, D.M.M., 2004). Sendo assim, deve ser considerado o período otimo de luz para que haja ´ o pleno desenvolvimento da planta e a obtençao de ˜ flores.
Como citado na seçao VI, devido ˜ | as caracter ` | ísticas do
morango, um contador no MSP430 deve ser acionado toda vez que o sensor LDR identificar luz.
Se o fotoperíodo da planta nao tiver sido conclu ˜ | ído,
sera acionado um LED de espectro completo pelo ´
canal K1 = 1 do modulo rel ´ | e, conectado a uma sa ´ | ída
do MSP430. Para o modo de economia de energia, este LED podera ser acionado apenas se o sensor ´
LDR nao identificar luminosidade. Quando conclu ˜ | | | ído
o fotoperíodo, K1 = 0 e o LED sera desacionado. ´
- Se todas as condiçoes acima estiverem de acordo, ˜
ocorrera o retorno do sistema ´ | a condiç ` | ao inicial e ser ˜ | á
realizada novamente a leitura dos dados dos sensores.
| IX. RESULTADOS

Foram realizados testes nos componentes individuais. O
conjunto da pastilha termica, aletas de alum ´ | ínio e os coolers
funcionaram de maneira impressionante. Entretanto, a temperatura referida no datasheet da pastilha (entre -30◦C e +70 ◦C) refere-se a temperatura interna da pastilha. O que significa ` que a temperatura em modulo nas aletas seria muito abaixo ´ destes valores e o ar resfriado seria ainda menor. Ainda assim, foi identificado um certo grau de aquecimento e resfriamento que serveriam para o proposito deste trabalho. O conjunto ´ completo, os coolers e a pastilha termica, estava consumindo ´ por volta de 7 A.

O LED de espectro completo funcionou de maneira apropriada e estava consumindo por volta 1 A da fonte de
alimentaçao. Uma ressalva quanto ao LED utilizado ˜ | e quanto ´
ao espectro de luz propiciado. O datasheet refere-se a este LED na cor branca (o que por definiçao possui o espectro completo ˜ da luz visível) enquanto o LED adquirido contempla a porçaõ entre o lilas e o azul deste espectro. Visto que as plantas ´ utilizam muito mais luz azul (maior energia) para realizar a fotossíntese, nao foram tomadas medidas corretivas. ˜

Foi realizada a mediçao de ripple nos level-shifters. Esta ˜ mediçao consistiu na montagem em protoboard do circuito ˜
level-shifter, na conexao de uma fonte vari ˜ | avel e da conex ´ | aõ
com o osciloscopio. As duas figuras abaixo mostram os ´ resultados destes testes.

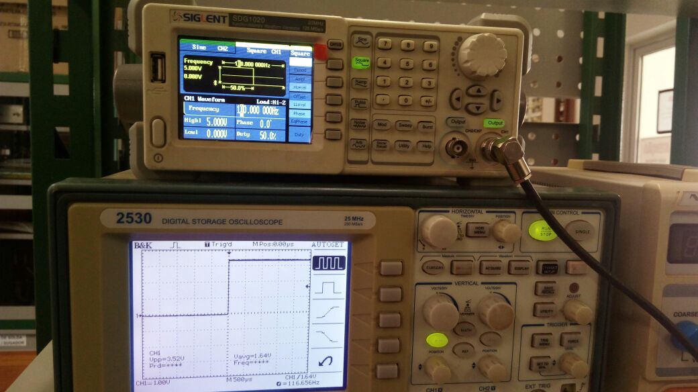
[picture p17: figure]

Fig. 16. Resultado de teste de ripple com 100 Hz.

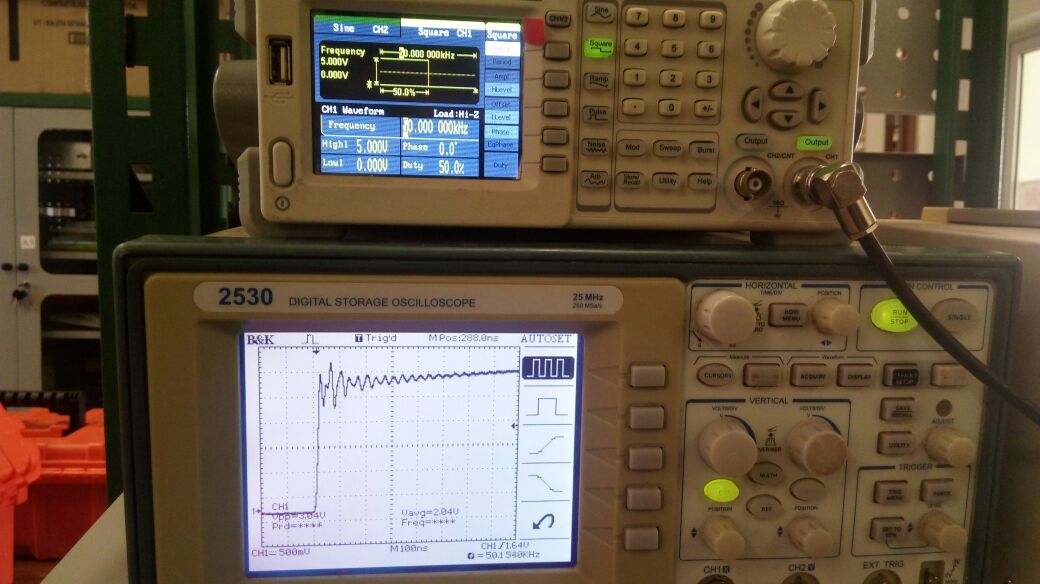
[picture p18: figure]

Fig. 17. Resultado de teste de ripple com 50 kHz.

De acordo com informaçao do fabricante, o tempo m ˜ | aximo ´
de switch (ou seja, para alterar de um nível logico para outro) ´
e de 20 ns. Ou seja, a frequ ´ | encia m ˆ | axima de operaç ´ | ao do ˜
componente BS170 e de 100 MHz. Como pode ser observado ´
na Fig. 17, ha oscilaç ´ | ao na banda passante ˜ | a partir de 50 kHz. `
Estas oscilaçoes n ˜ | ao ir ˜ | ao interferir neste projeto mas devem ˜
ser cuidadosamente tratadas quando aplicado o componente
BS170 em projetos com shift de clock ou temporizaçao cr ˜ | ítica.
| Foi realizado teste de tensao na sa ˜ | | ída do regulador de
tensao 7805 e dos level-shifter. Neste teste, conectou-se as ˜ pontas de prova de um multímetro no regulador 7805 para
medir a tensao de sa ˜ | ída, 5V como esperado, e nas saídas dos
level-shifters quando realizados comandos com o MSP430.
Nestas mediçoes, as sa ˜ | ídas de tensao do MSP430 -¿ level- ˜
shifter estavam por volta de 5V e 6V. Abaixo segue o es-
quematico do regulador de tens ´ | ao utilizado para reduzir de ˜
12V para 5V. O uso dos capacitores foi para reduzir o ripple no ground.

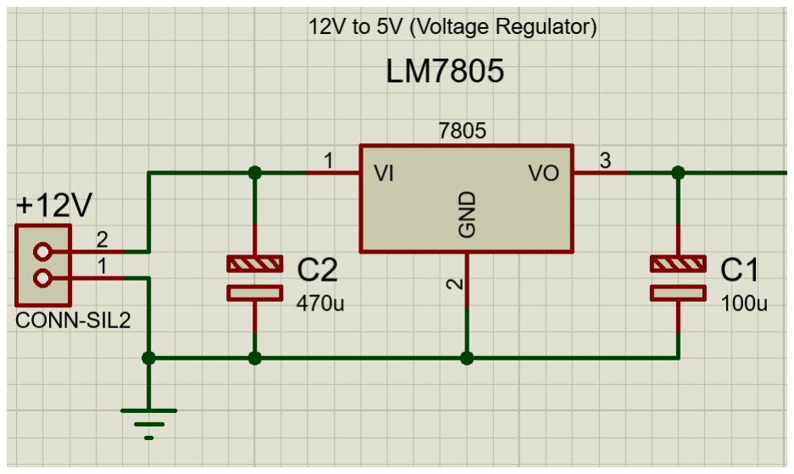
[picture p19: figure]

Fig. 18. Esquematico do regulador de tens ´ | ao utilizando o LM7805. ˜
Foi realizado teste de logica de sa ´ | ídas com o MSP430
utilizando reles e LED’s. Nesta etapa, n ´ | ao foram conectados os ˜
atuadores visando a segurança destes componentes. Tambem´ foram realizados testes com o sensor DHT11 no MSP430, o que nos retornou temperatura ambiente por volta de 0x19 (25

◦C). O LM393 do sensor de umidade do solo fora calibrado nesta etapa de teste para descer para nível logico baixo quando ´
a tensao de sa ˜ | ída do comparador fosse entre 1V e 2,5V, o
que indica situaçao de pouca umidade no solo. N ˜ | ao foram ˜
realizados testes posteriores com os demais sensores.

Quando montado o circuito completo e ligados todos os componentes, foram identificados problemas de curto-circuito na fonte e power shortage. Uma possível explicaçao para ˜ este problema e o fato do componente LM7805 possuir um ´ limite de corrente que nao permite que todos os componentes ˜ estejam ligados ao mesmo tempo. Este problema poderia ter sido solucionado quando utilizado mais de um regulador
de tensao, o que n ˜ | ao foi realizado. Outra melhoria para o ˜
circuito regulador de tensaõ e o uso de dissipadores de calor ´ nos reguladores de tensao para evitar o superaquecimento do ˜ componente quando submetido a corrente proximas a de seu ´ limite de operaçao. ˜
A prototipaçao da PCB n ˜ | ao foi realizado devido ao elevado ˜
custo de manufatura e a baixa qualidade de um prototipo no ´ país. Foram averiguadas empresas no exterior que pudessem realizar este serviço mas o tempo de entrega excedia em muito o limite de tempo para entrega deste trabalho. Uma
prototipaçao artesanal deste layout estava fora de quest ˜ | ao por ˜
possuir trilhas muito pequenas e proximas umas das outras. A ´
nao prototipaç ˜ | ao da PCB dificultou muito a etapa de debugging ˜
do circuito, ja que este fora montado na protoboard. Problemas ´
a serem elencados desta montagem sao a organizaç ˜ | ao da ˜
protoboard, trilhas com mau contato e aquecimento das trilhas de entrada 12V.
X. CONCLUSOES ˜
Por fim, ate a data de redaç ´ | ao deste relat ˜ | orio o projeto ´
nao mostrou-se 100% funcional. Como melhorias podemos ˜ elencar:
- | Melhor debugging do codigo e melhora na l ´ | ogica do ´
codigo; ´
- | Melhora na modularizaçao das funç ˜ | oes de leitura dos ˜
sensores;
- | Prototipaçao da PCB e melhor organizaç ˜ | ao dos cir- ˜
cuitos;
- | Melhor temporizaçao do sistema quanto ˜ | a leitura dos `
dados dos sensores;
- Uso de um cano de PVC branco para acomodaçao da ˜ muda e para facilitar a irrigaçao; ˜
- Uso de uma bomba submersa para adquirir a pressaõ
ideal da agua no tubo que vai de encontro ´ | a v ` alvula ´
solenoide (o que resultaria em um custo mais elevado ´ de projeto);
- | Melhor pesquisa quanto a quantidade necess ` | aria de ´
agua para irrigaç ´ | ao; ˜
- Poderia ser efetuada uma melhor sinergia entre os dados de umidade do solo e umidade relativa do ar
para efetuar o calculo da quantidade ideal de ´ | agua a ´
depender da condiçao atual do ambiente e do clima ˜ na regiao em que a estufa se encontra; ˜
- Poderia ser utilizado um sensor de pH da agua para ´
indicar situaçao n ˜ | ao saud ˜ | avel para planta de acordo ´
com o pH (o que tambem resultaria em um custo mais ´ elevado de projeto); e
- Melhor planejamento, por parte dos autores, do tempo disponível de projeto.

Apesar dos resultados, o conhecimento adquirido no decor-
rer deste projeto foi proveitoso e sera utilizado como refer ´ | encia ˆ
para pesquisas e projetos futuros. Os autores deste trabalho planejam dar continuidade a este projeto o qual sera com- ´ plementado ao longo do tempo, ainda que estudos posteriores fujam do escopo da materia ´ a qual este projeto final se destina. `

AGRADECIMENTOS

Os autores gostariam de agradecer aos colegas:

Mariana Costa Dias, Doutoranda em Bioinformatica e ´ Mestre em Biologia Vegetal sub-area Fisiologia Vegetal pela ´ UFMG; pela consultoria e pela indicaçao de artigos relaciona- ˜ dos a fisiologia das plantas e do morango. `

Arthur Pereira Wernke, Graduando em Engenharia Aeroespacial pela UnB - FGA; pelo auxílio no uso do compilador
LATEXe pela assistencia nos c ˆ | alculos de transporte de calor. ´

Victor Menezes Ribeiro, Graduando em Engenharia Aeroespacial pela UnB - FGA; pelo auxílio nos CAD’s da estrutura e plantas de corte do compartimento para eletronica. ˆ

Josias Diego Martins, Engenheiro da Bobsien P&D; pelo
trabalho realizado no topico deste relat ´ | orio e pela sugest ´ | ao do ˜
uso do efeito Peltier para aquecimento/resfriamento da estufa.

REFERENCES

[1] H. Kopka and P. W. Daly, A Guide to LATEX, 3rd ed. Harlow, England: Addison-Wesley, 1999.
[2] ROMANINI, Carlos E. B. et al. Desenvolvimento e simulaçao de ˜ um sistema avançado de controle ambiental em cultivo protegido. Rev. Bras. Eng. Agríc. Ambient., [s.l.], v. 14, n. 11, p.1194-1201, 2010. FapUNIFESP (SciELO).
[3] | RURALNEWS, Redaçao. ˜ | Estufas - produçao agr ˜ | ícola em ambientes
| controlados.2015.
Disponível em: http://www.ruralnews.com.br/visualiza.php?id=202.
[4] ARAGUAIA, Mariana. Morango; Brasil Escola.
Disponível | em: | hhttp://brasilescola.uol.com.br/frutas/morango.htm.
Acesso em 31 de setembro de 2017.
[5] PALHA, Maria da Graça. Manual do Morangueiro; 2005.
[6] | Morato, J., Cruz, S., Pereira, .F, Metrolho, J. C.. ˆ | Multi-Monitorizaçaõ
de Estufas Agrícolas. Escola Superior de Tecnologia. Escola Superior
Agraria. Instituto Polit ´ | ecnico de Castelo Branco. ´
[7] | SOUSA, Andre Luiz C. N. D. e BUSSON, Bruna O.. ´ | | Projeto de Sistema
| de Irrigaçao para Unidade de Agricultura Familiar ˜ | | . 2016.
[8] | SCARPARE, Joao Alexio Filho. ˜ | Vernalizaçao em cinco cultivares de ˜
| morangueiro. 2007.
[9] HENZ, Gilmar P.; Desafios enfrentados por agricultores familiares na
| produçao de morango no Distrito Federal ˜ | . 2010.
[10] | Texas | Instruments. LM393, LM293, LM193, LM2903 Dual
Differential Comparators datasheet. October, 1979.
[11] ON Semiconductor. BS170 — Small Signal MOSFET datasheet,
| Rev.7. November, 2017.
[12] AOSONG. ”Temperature and humidity module — DHT11 Product
| Manual”. s.d.
[13] Foton Ukraine. 3W High Power LED datasheet. [entre 2011 e 2017].

[14] | Texas | Instruments. µA7800 SERIES — POSITIVE-VOLTAGE
REGULATORS datasheet, Revised May 2003. May 1976.
[15] Texas Instruments. Interfacing the 3-V MSP430 to 5-V Circuits. October 2002.
[16] Texas Instruments. Mixing C and Assembler With the MSP430. March 2002.
[17] BRAGA, Newton C. Dissipadores de calor (ART208).
Disponível | em: | http://www.newtoncbraga.com.br/index.php/
como-funciona/1405-art208. Acesso em: 30 out. 2017.

ANEXOS

- Diagrama Logico ´

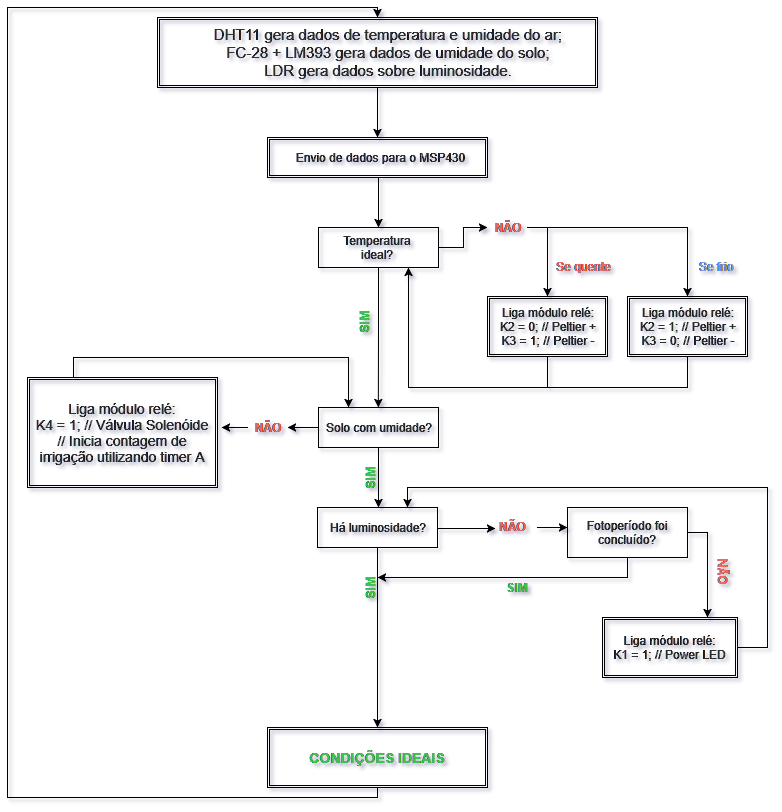
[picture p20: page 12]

- Codigo ´
1 | # i n c l u d e <msp430 . h>
2 | # i n c l u d e <msp430g2553 . h>

3
4 | /∗ ==============================
5 | ∗ DECLARACAO DE CONSTANTES
6 | ∗ −−−−−−−−−−−−−−−−−−−−−−−−−−−−−∗ /

7
8 | /∗ MODULO RELE −> SAIDAS ∗/
9 | # d e f i n e K1 BIT0 / / K1 = P1 . 0
10 | # d e f i n e K2 BIT1 / / K2 = P1 . 1
11 | # d e f i n e K3 BIT2 / / K3 = P1 . 2
12 | # d e f i n e K4 BIT3 / / K4 = P1 . 3

13
14 | # d e f i n e LED BIT6 / / LED = P1 . 6

15
16 | /∗ SENSORES −> ENTRADAS ∗/
17 | # d e f i n e LDR BIT4 / / LDR = P1 . 4
18 | # d e f i n e UMI BIT5 / / UMI = P1 . 5
19 | # d e f i n e DHTPIN BIT7 / / DHT11 = P1 . 7

20
21 | /∗ =================================== ∗/

22
23 | /∗ ===================================
24 | ∗ VARIAVEIS GLOBAIS
25 | ∗ PROTOTIPOS DE FUNCOES
26 | ∗ −−−−−−−−−−−−−−−−−−−−−−−−−−−−−−−−−−−∗ /

27
28 | /∗ DHT 11 ∗/
29 | u n si g n e d c h a r v o l a t i l e TOUT;
30 | u n si g n e d c h a r v o l a t i l e SECOND TIMER= 0;

31
32 | u n si g n e d c h a r d a t a [ 5 ] ;

33
34 | v oi d a c o r d a ( v oi d ) ;
35 | u n si g n e d c h a r r e s p o s t a ( v oi d ) ;
36 | u n si g n e d c h a r l e r B y t e ( v oi d ) ;
37 | u n si g n e d c h a r c h e c k P a r i d a d e ( u n si g n e d c h a r
| ∗) ;

38
39 | /∗ =================================== ∗/

40
41 | # p ragma v e c t o r = TIMER0 A0 VECTOR
42 | i n t e r r u p t v oi d CCR0 ISR ( v oi d ) {
43 | SECOND TIMER++;
44 | TOUT= 1;
45 | TACCTL0 &= ˜ ( CCIFG ) ;
46 | / / BIC SR IRQ ( LPM0 bits ) ;
47 | }

48
49 | /∗ ===================================
50 | ∗ PROGRAMA PRINCIPAL
51 | ∗ −−−−−−−−−−−−−−−−−−−−−−−−−−−−−−−−−−−∗ /
52 | v oi d main ( v oi d ) {
53 | WDTCTL = WDTPW + WDTHOLD;

54
55 | /∗ DECLARA ENTRADAS E SAIDAS ∗/
56 | P1DIR |= K1 + K2 + K3 + K4 ;
57 | P1OUT |= ( K1 + K2 + K3 + K4 ) ;

58
59 | P1REN |= (UMI + DHTPIN ) ;
60 | P1OUT |= (UMI + DHTPIN ) ;

61
62 | /∗ CONFIGURACAO DO CONVERSOR AC ∗/
63 | ADC10CTL1 = INCH 1 + ADC10DIV 3 ;
64 | ADC10CTL0 = ADC10SHT 3 + ADC10ON +
| ADC10IE ;

65
66 | /∗ CONFIGURACAO DO TIMER ∗/
67 | BCSCTL1 = CALBC1 1MHZ;
68 | DCOCTL = CALDCO 1MHZ;

69
70 | TACCR0 = 5 0 0 0 0;
71 | TACCTL0 = CCIE ;
72 | TA0CTL = TASSEL 2 + ID 2 + MC 1 +

TACLR;
73 | e n a b l e i n t e r r u p t ( ) ;

74
75 | LPM1;

76
77 | P1OUT |= K2 ;
78 | P1OUT &= ˜ ( K3 ) ;

79
80 | w hil e ( 1 ) {

81
82 | /∗ INTERFACE COM DHT11 ∗/
83 | i f (SECOND TIMER >= 5 ) {
84 | b i c S R r e g i s t e r o n e x i t (
| LPM3 bits ) ;
85 | a c o r d a ( ) ;
86 | i f ( r e s p o s t a ( ) ) {
87 | d a t a [ 0 ] = l e r B y t e ( ) ;
88 | d a t a [ 1 ] = l e r B y t e ( ) ;
89 | d a t a [ 2 ] = l e r B y t e ( ) ;
90 | d a t a [ 3 ] = l e r B y t e ( ) ;
91 | d a t a [ 4 ] = l e r B y t e ( ) ;
92 | }

93
94 | i f ( c h e c k P a r i d a d e ( d a t a ) ) {
95 | P1OUT |= LED;
96 | } e l s e {
97 | P1OUT &= ˜ ( LED ) ;
98 | | b r e a k ;
99 | }

100
101 | i f ( d a t a [ 2 ] >= 0 x10 ) {
102 | P1OUT |= K2 ;
103 | P1OUT &= ˜ ( K3 ) ;
104 | } e l s e {
105 | i f ( d a t a [ 2 ] <= 0 x16 ) {
106 | P1OUT |= K3 ;
107 | P1OUT &= ˜ ( K2 ) ;
108 | } e l s e {
109 | P1OUT |= ( K2 + K3 ) ;
110 | }
111 | } /∗ fim do i f −e l s e ∗/

112
113 | i f ( ( P1IN & BIT4 ) == 0 ) P1OUT &= ˜
K1 ;
114 | i f ( ( P1IN & UMI ) == 0 ) P1OUT &= ˜
K4 ;

115
116 | / / SUB−ROTINA ASSEMBLY
117 | asm | ( ”mov .w & | P1IN , R15 \n ”
118 | ” and . b # 0 8 ,R15 \n ”
119 | ” j z . umi da deBai xa \n ”
120 | ” jmp . fim \n ”

121
122 | ” . umi da deBai xa : \n ”
123 | ” and . b #F7 ,& | P1OUT \n ”
124 | ”mov .w #FF , R14 \n ”
125 | ”mov .w #FF , R13 \n ”
126 | ”mov .w #3F , R12 \n ”
127 | ” jmp . c o nta gem 0 \n ”

128
129 | ” c o nta gem 0 : \n ”
130 | ” s u b . b # 1 ,R14 \n ”
131 | ” j z . c o nta gem 1 \n ”
132 | ” jmp . c o nta gem 0 \n ”

133
134 | ” . c o nta gem 1 : \n ”
135 | ” s u b . b # 1 ,R13 \n ”
136 | ” j z . c o nta gem 2 \n ”
137 | ”mov .w #FF , R14 \n ”
138 | ” jmp . c o nta gem 0 \n ”

139
140 | ” . c o nta gem 2 : \n ”
141 | ” s u b . b # 1 ,R12 \n ”
142 | ” j z . fim \n ”
143 | ”mov .w #FF , R14 \n ”

144 | ”mov .w #FF , R13 \n ”
145 | ” jmp . c o nta gem 0 \n ”

146
147 | ” . fim : \n ”
148 | ” c l r . b R15 \n ”
149 | ” c l r . b R14 \n ”
150 | ” c l r . b R13 \n ”
151 | ” c l r . b R12 \n ” ) ; ∗ /

152
153 | TACTL |= TACLR;
154 | TA0CTL |= 0 x10 ;
155 | TACCR0 = 5 0 0 0 0;
156 | SECOND TIMER = 0 ;
157 | /∗ fim da i n t e r f a c e com o DHT11
| ∗/
158 | } /∗ fim do i f −e l s e ( s e c o n d t i m e r )
| ∗/
159 | } /∗ fim do w hil e ∗/
160 | } /∗ FIM DO PROGRAMA PRINCIPAL ∗/

161

162
163 | /∗ ===================================
164 | ∗ FUNCOES DO DHT11
165 | ∗ −−−−−−−−−−−−−−−−−−−−−−−−−−−−−−−−−−−∗ /
166 | u n si g n e d c h a r l e r B y t e ( ) {
167 | TOUT = 0 ;
168 | u n si g n e d c h a r numero = 0 ;
169 | u n si g n e d c h a r i ;
170 | TACCTL0 &= ˜ ( CCIE ) ;
171 | f o r ( i = 8; i >0; i −−){
172 | w hil e ( ! ( P1IN & DHTPIN ) ) ;
173 | TACTL |= TACLR;
174 | TA0CTL |= 0 x10 ;
175 | TACCTL0 |= CCIE ;
176 | w hil e ( ( P1IN & DHTPIN ) ) ;
177 | TA0CTL &= ˜ ( 0 x30 ) ;
178 | i f (TAR > 1 3 )
179 | numero |= 1 << ( i −1) ;
180 | }
181 | r e t u r n numero ;
182 | } /∗ fim l e r B y t e ∗/

183
184 | u n si g n e d c h a r r e s p o s t a ( ) {
185 | TOUT= 0;
186 | TACTL |= TACLR;
187 | TACCR0 = 2 5;
188 | TACCTL0 |= CCIE ;
189 | w hil e ( ! ( P1IN & DHTPIN ) && !TOUT) ;
190 | i f (TOUT)
191 | r e t u r n 0 ;
192 | e l s e {
193 | TACTL |= TACLR;
194 | TACCTL0 |= CCIE ;
195 | w hil e ( ( P1IN & DHTPIN ) && !TOUT) ;
196 | i f (TOUT)
197 | r e t u r n 0 ;
198 | e l s e {
199 | TACCTL0 &= ˜ ( CCIE ) ;
200 | r e t u r n 1 ;
201 | }
202 | } /∗ fim do i f −e l s e ∗/
203 | } /∗ fim r e s p o s t a ∗/

204
205 | v oi d a c o r d a ( ) {
206 | P1DIR |= DHTPIN ;
207 | P1OUT &= ˜ ( DHTPIN ) ;
208 | d e l a y c y c l e s ( 2 5 0 0 0 ) ;
209 | P1OUT |= DHTPIN ;
210 | d e l a y c y c l e s ( 3 0 ) ;
211 | P1DIR &= ˜ ( DHTPIN ) ;
212 | } /∗ fim a c o r d a ∗/

213
214 | u n si g n e d c h a r c h e c k P a r i d a d e ( u n si g n e d c h a r
| ∗ d a t a ) {
215 | i f ( d a t a [ 4 ] != ( d a t a [ 0 ] + d a t a [ 1 ] +

d a t a [ 2 ] + d a t a [ 3 ] ) ) {
216 | r e t u r n 0 ;
217 | }
218 | e l s e r e t u r n 1 ;
219 | } /∗ fim c h e c k P a r i d a d e ∗/

220

221

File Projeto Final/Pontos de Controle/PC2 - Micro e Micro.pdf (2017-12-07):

# Estufa Agrícola Automatizada com Auxílio do MSP430 para Cultivo de Morangos

Arthur Evangelista dos Santos Universidade de Brasília, Faculdade do Gama UnB, FGA Matrícula: 14/0016686
Email: arthuevangelista@hotmail.com

Gabriela Conceio dos Santos Universidade de Brasília, Faculdade do Gama UnB, FGA Matrícula: 16/0152038
Email: gabrielacsantos.engunb@gmail.com

Abstract—Este projeto visa criar um prototipo de estufa ´ agrícola automatizada para o cultivo de morangos aplicando sensores eletronicos para controlar as condies de umidade e ˆ temperatura com auxílio do microcontrolador MSP430.

Keywords—MSP430, microcontrolador, automaçao, morangos, ˜ estufa.

I. REVISAÕ BIBLIOGRAFICA ´
A. O Morangueiro

O morangueiro pertence a Família Rosaceae. De origem Europeia, as plantas cultivadas para o consumo de sua fruta ´ sao o resultado de um sucessivo trabalho de melhoramento ˜
genetico e cruzamento entre algumas esp ´ | ecies do G ´ | enero ˆ
Fragaria. Atualmente, existem mais de 15 variedades de morangueiros. E um vegetal rasteiro, de caule do tipo estolho, ´ produzindo gemas que permitem com que novas plantas, com raízes e folhas, sejam formadas, assexuadamente. Uma imagem do morangueiro encontra-se abaixo na Fig. 1. No Brasil, sua produçaõ e mais significativa nos meses de junho a dezembro ´
e requer boa umidificaçao do solo. Por este motivo, ˜ | acaros e ´
pulgoes s ˜ | ao suas principais pragas. ˜


Fig. 1. Morangueiro

Desta planta origina-se o morango (Fig. 2), cuja parte
vermelha, comestível, e, na verdade, o recept ´ | aculo floral de- ´
senvolvido. Assim, ele e um pseudofruto; sendo os frutos, do ´ tipo aquenio, as estruturas amarronzadas que se encontram ˆ incrustadas nele.


Fig. 2. Fruto e pseudofruto do morango

Características gerais do cultivo do morango
:
- Clima: Locais com temperatura alta durante o dia e baixa durante a noite sao considerados bons para o ˜ cultivo do morangueiro. O calor e importante para o ´ crescimento vegetativo das plantas, enquanto o frio é
imprescindível a frutificaçao. A floraç ˜ | aõ e favorecida ´
por temperaturas abaixo de 10 ◦C e desfavorecida por temperaturas acima de 25 ◦C. O comprimento do
dia, ou seja, o numero de horas de luz, tamb ´ | | em tem ´
influencia sobre a produç ˆ | ao. A estas caracter ˜ | ísticas é
dado o nome de fotoperíodo.
- Sistemas de cultivo: O morango pode ser cultivado em
canteiros a ceu aberto, em estufas e em combinaç ´ | | aõ
com o uso de tunel baixo. Atualmente est ´ | | a sendo ´
implantado o sistema de cultivo hidroponico. ˆ
- Local de plantio: O morangueiro produz melhor em solos areno-argilosos e bem drenados. As areas devem ´
ser de facil acesso e ter bom suprimento de ´ | | agua ´
para irrigaçao. Deve ser evitado o plantio em local ˜ recentemente cultivado com tomate, batata, fumo ou
com o proprio morango. H ´ | a de se pesquisar sobre ´
outros metodos que tornem poss ´ | | ível o plantio de
culturas morangos no mesmo local. Tambem deve ser ´ evitado o plantio em terras de baixa umida. ´
- Período de plantio: A epoca de plantio varia de acordo ´
com a regiao e a cultivaç ˜ | ao a ser plantada. De um ˜
modo geral, planta-se de janeiro a maio. Em regioes ˜
mais quentes, a epoca recomendada ´ | e de abril a ´

maio. Em locais com altitude acima de 1.000 metros, as cultivares de dia neutro podem ser plantadas até setembro.

- | Irrigaçao: A irrigaç ˜ | ao do morangueiro pode ser feita ˜
por aspersao, por ˜ | em o gotejamento (fertirrigaç ´ | ao) tem ˜
sido mais eficiente e economico. Por este motivo, ˆ
neste trabalho sera utilizado o m ´ | etodo de irrigaç ´ | aõ
por gotejamento. Geralmente irriga-se tres vezes por ˆ semana e com duraçao de 30 a 45 minutos, evitando ˜ o excesso de agua. ´
B. O Morangueiro no Distrito Federal

A cultura do morangueiro iniciou-se no Distrito Federal em meados da decada de 70, tendo sido primeiramente introduzida ´ e conduzida de forma empírica pelos agricultores de origem
japonesa vindos da regiao de Atibaia, S ˜ | ao Paulo, at ˜ | e hoje o ´
principal polo de produç ´ | ao de morango naquele estado. ˜

Estes agricultores pioneiros vieram iniciar o cultivo de hortaliças e de frutas para abastecer o novo mercado do Planalto Central. Muitos foram assentados pelo Instituto Nacional de Colonizao e Reforma Agraria - INCRA, a partir ´ de 1970, no ”Projeto Integrado de Colonizaçao Alexandre ˜
Gusmao (PICAG)”, na Regi ˜ | ao Administrativa de Brazl ˜ | andia, ˆ
atualmente o principal produtor de morango do Distrito Federal.

A cultura do morango adaptou-se muito bem as condies climaticas e de solo do Planalto Central, que apresenta altitude ´
de aproximadamente 1000 metros. Alem disso, essa regi ´ | aõ
possui temperaturas mais altas no verao, que favorecem a ˜
produçao de mudas e na sequ ˜ | encia passa por um inverno ˆ
ameno e seco, o que auxilia no período de florao, frutificaçaõ e melhora de forma significativa a qualidade dos frutos cultivados.
Segundo a Emater-DF (Empresa de Assistencia T ˆ | ecnica ´
e Extensao Rural do Distrito Federal), no ano de 2016, a ˜ safra de morangos no Distrito Federal alcançou cerca de 5250 toneladas, numeros que colocam o Distrito Federal na disputa ´ do sexto lugar da produçao nacional entre os estados produ- ˜
tores da fruta . Sao, em m ˜ | edia, 240 produtores de morango ´
em todo o DF. Desses, 35% de produtores agrícolas da cidade sao os que distribuem o que se consome no DF. ˜
C. Estufas Agrícolas

Em grande parte da historia da humanidade, fomos ´ caçadores-coletores. Ha cerca de 10.000 anos, começamos a ´ domesticar plantas e animais como uma forma de tornar a nossa oferta de alimentos mais acessível e previsível.

Sendo assim, para melhorar a produçao agr ˜ ícola, surgiram as estufas agrícolas. O objetivo do cultivo agrícola em estufas
e proporcionar um ambiente controlado, em relaç ´ | ao a fatores ˜
climaticos como temperatura, umidade, luz e quantidade de ´ agua (rega), para que as plantas possam ter um crescimento ´ em um ambiente ideal (Silva, 1976).

A estrutura de uma estufa agrícola depende bastante de
sua finalidade. Geralmente, e constitu ´ | ída por uma armaçao, ˜
de alumínio ou outro material resistente, com uma altura suficiente para poder cultivar e caminhar dentro sem incomodos, ˆ
ela e coberta por um pl ´ | astico transparente, em alguns casos ´
possui uma tela, conhecida como sombrite, que auxilia na regulagem da temperatura interna da estufa alem de ventiladores ´ e em alguns casos lampadas para o controle de luminosidade ˆ (Fig. 3).


Fig. 3. Estrutura de uma estufa convencional para o cultivo de morangos

O aumento significativo da utilizaçao de estufas se deu, ˜
em parte, pela criaçao do pl ˜ | astico, devido ao seu baixo custo e ´
versatilidade, porem existem outros fatores que influenciam tal ´ fato, como o melhor desenvolvimento do plantio, aumento de produtividade, colheita nas entressafras e produtos de melhor qualidade.
D. Automaçao de Estufas ˜

Em uma estufa existem diversas variaveis que podem ser ´ monitoradas e verificadas para o controle do plantio, como temperatura, umidade e luminosidade. Considerando o ponto de vista dos produtores agrícolas, a correta leitura dos dados e posterior tomada de decisao pode trazer resultados satis- ˜ fatorios. ´

A automatizaço de uma estufa ˜ | | e uma excelente ferramenta ´
de auxílio ao agricultor, pois permite a tomada de deciso no ˜
momento certo, conforme a analise das vari ´ | aveis verificadas. ´

II. JUSTIFICATIVA

Apesar de ser considerado um dos maiores produtores de morango do Brasil, durante o de 2017, o Distrito Federal veio enfrentando um grave crise hídrica, o que afetou de
forma significativa a produçao de morangos nessa regi ˜ | ao. ˜
Segundo dados da Emater, a restriçao no abastecimento de ˜
agua provocou a diminuiç ´ | ao da ˜ | area plantada em cerca de ´
30%, de 150 hectares em 2016 para 105 hectares neste ano.
Alem disso, a desaceleraç ´ | ao na produç ˜ | ao de mercado de ˜
morangos do DF ocasionou a diminuiçao do n ˜ | umero de tra- ´
balhadores envolvidos direta e indiretamente com a atividade, gerando a queda na renda das famílias e do Produto Interno Bruto(PIB) do Morango.

Diante disso, a escolha do projeto de construçao de uma ˜ estufa automatizada foi motivada pela simples possibilidade de se oferecer uma nova alternativa para o melhoramento do cultivo de morangos no Distrito Federal , uma vez que a estufa proposta sera capaz de controlar todas as necessi- ´ dades da cultura e o ambiente da estufa, o que proporcionará aos produtores mais qualidade em seus frutos e uma maior
renda. Tambem ser ´ | a poss ´ | ível controlar a quantidade de agua ´
utilizada na irrigaçao da plantaç ˜ | | ao gerando, consequentemente, ˜
economia de recursos hídricos e financeiros na produçao de ˜ morangos.

III. OBJETIVOS

Considerando que cada especie de planta necessita de ´
situaçoes clim ˜ | aticas diferentes e espec ´ | íficas para se desen-
volver, o projeto proposto tem o intuito de otimizar o cultivo de morangos atraves do desenvolvimento de uma estufa capaz de ´ gerenciar (monitorar e atuar) o controle das condiçoes ambien- ˜
tais dentro do ambiente da estufa atraves da disponibilizaç ´ | aõ
de recursos de automaçao como irrigaç ˜ | ao autom ˜ | atica, sistemas ´
de ventilaçao, iluminaç ˜ | ao e controle de temperatura ambiente, ˜
utilizando o microcontrolador MSP430.

Em resumo, os objetivos deste trabalho so:

- | Economia de agua devido a automaç ´ | ao do ambiente; ˜
- Captao de dados de umidade e temperatura ambiente;
- Captao de dados de umidade do solo;
- Controle de irrigaçao da estufa; ˜
- | Controle da iluminaçao e do fotoper ˜ | íodo da planta;
- Controle da temperatura no ambiente interno da estufa;
- Apresentaçao dos dados adquiridos pelos sensores ao ˜ usuario. ´

IV. ESTRUTURA

A estrutura do prototipo da estufa foi inicialmente con- ´ struída com canos PVC (Policloreto de Vinila) de 25 mm de
diametro, e coberta com filme pl ˆ | astico transparente. A escolha ´
desses materiais foi feita pois se tratam de materiais resistentes, acessíveis, de baixo custo e suprem bem as necessidades de controle do mini-ecossistema da estufa.

As dimensoes da estruturas foram determinadas a partir da ˜ densidade de plantio estipulada para o cultivo do morangueiro em estufas, onde esta define que o espaamento entre os morangueiros deve ser de no mínimo 20 cm e altura maxima ´ que a planta pode atingir 30 cm.

V. VISAÕ GERAL DO SISTEMA

O sistema do projeto proposto pode ser dividido duas partes. Uma parte de hardware, dotado do microcontrolador
MSP430, sensores eletronicos, os quais s ˆ | ao encarregados pela ˜
aquisiçao de dados do sistema, e atuadores, respons ˜ | aveis por ´
irrigar, iluminar, ventilar e reduzir ou aumentar a temperatura. E uma parte de software, responsavel pelo processamento dos ´ dados e do controle dos perifericos atuadores. ´


Fig. 4. Vista Isometrica do CAD da Estrutura realizada no software CATIA. ´

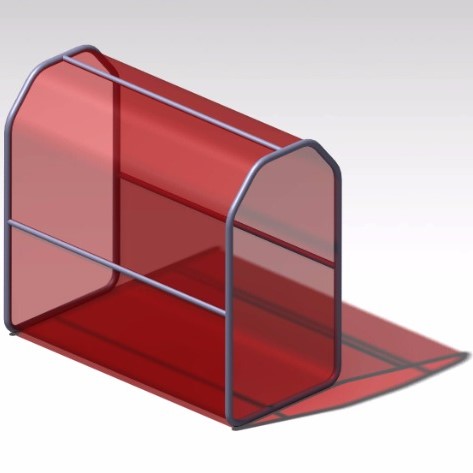
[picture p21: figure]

Fig. 5. Render da Estrutura.


Fig. 6. Estrutura construída em cano PVC.

A. Hardware
1) Lista de Componentes:
- MSP-EXP430G2553LP;
- Sensor de luz (LDR 5mm);
- Sensor de temperatura e umidade (DHT11);
- Resistores de 10kOhm;
- Transistor Mosfet BS170;
- Modulo sensor de umidade do solo (Umidostato); ´
- | Modulo rel ´ | e 4 canais; ´
2) Descriçao do Hardware: ˜
- | Level-shifter para reduçao de tens ˜ | ao: ˜ | Uma mon-
tagem utilizando dois resistores de 10k ohm e um transistor mosfet BS170. O level-shifter reduz a tensaõ para que seja possível conectar componentes que
| utilizam diferentes tensoes como n ˜ | ível logico alto. Se ´
um sinal chega com 3,3 V o level-shifter subira esta ´
tensao para 5 V em sua sa ˜ | ída para que seja utilizado
| por outro componente.
| A recíproca e verdadeira. Portanto, se um sinal tiver ´
| 5 V, a saída do level-shifter tera 3,3 V. Testes foram ´
realizados com este componente para verificar se ele
| funciona e quais os níveis de tensao em sua sa ˜ | | ída.
| Houve tambm uma preocupaçao quanto a frequ ˜ | | encia ˆ
maxima de operaç ´ | ao, uma vez que este componente ˜
sera utilizado na sa ´ | ída de todos os sensores e nas
saídas do MSP430. Foi confirmada o nível de ruído apresentado na saída do level-shifter a partir de 5MHz, o que ratifica a informaçao fornecida pelo datasheet ˜ do componente transistor BS170.
O esquematico desta montagem encontra-se na Fig. 7 ´ abaixo.

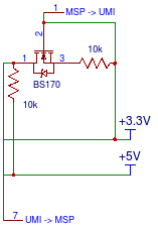
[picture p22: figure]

Fig. 7. Esquematico da unidade ´ | level-shifter (redutora de tensao). ˜
- | Modulo rel ´ | e 4 canais: ´ | Sera utilizado um m ´ | odulo com ´
4 reles para controle dos dispositivos com tens ´ | ao de ˜
12V ou com correntes superiores a suportada pelo
| MSP430;
- Modulo sensor de umidade do solo (umidostato): ´ Possui formato de garfo (apenas duas pontas que devero estar fincadas no solo). Ao identificar umidade
| ocorrera uma diferença de potencial entre as pontas ´
do garfo. A corrente que passara entre as duas pontas ´
e muito pequena (resist ´ | encia pr ˆ | oxima dos M ohm). ´
Quanto maior a resistencia, menor a umidade entre as ˆ ponteiras. A corrente, portanto, e muito baixa para que ´ se insira o sensor diretamente na porta analogica do ´
micro. E necess ´ | ario o uso de um m ´ | odulo comparador. ´
Nada mais e que um amplificador operacional em ´ modo comparador. Quando comprado o sensor, o comparador LM393 (low offset voltage dual comparator) vem no conjunto.
A tensao de trabalho ˜ | e de 3,3 V a 5 V. O comparador ´
tem quatro pinos: Vcc, GND, D0 (digital) e A0
| (analogico). Para usar a sa ´ | | | ída digital foi necessario ´

utilizar o potenciometro j ˆ | a encontrado no m ´ | odulo para ´
calibrar o sensor.
O potenciometro ir ˆ | a ajustar em qual medida de umi- ´
dade a saída digital tera n ´ ível logico zero. Podemos ´ utilizar uma entrada digital do MSP430 ativa em alta para identificar quando a umidade esta baixa. Ou seja, ´ Quando D0 = 1 a umidade esta baixa. Quando D0 = ´
0, ha umidade suficiente, n ´ | ao h ˜ | a necessidade de ligar ´
o irrigador (valvula solen ´ | oide). ´
Utilizaremos apenas o pino digital para o projeto. A leitura dos dados de umidade do solo podem ser comutados com a leitura dos dados de umidade do ar (DHT11), liberando a porta digital para outra aplicaçao. ˜
Utilizar uma porta analogica para leitura de dados ´ seria mais preciso, mas exigira um processamento do ´ sinal analogico antes deste ser inserido no microcon- ´ trolador (tecnicas de amostragem do sinal, uso do ´
criterio de Nyquist e o uso de uma m ´ | edia m ´ | ovel ou ´
filtro digital para evitar ruído ou sinais aleatorios ´ | ).
- Display de Cristal Líquido: Para visualizaço dos ˜ dados (umidade do ar, umidade do solo e temperatura) sera utilizado um display. Dependendo da temperatura ´ sera ativado um exaustor (ventilar a estufa) e uma ´ pastilha termica (aquece ou resfria o ambiente da est- ´
ufa). Da umidade do ar/solo serao ligadas as v ˜ | alvulas ´
de irrigaçao. ˜
Possui uma biblioteca na IDE do arduino: (#include¡LiquidCrystal.h¿) e pode ser facilmente implementada no MSP430 utilizando algoritmos disponíveis na documentaçao do fabricante. O display ˜
sera meramente utilizado para refer ´ | encia do usu ˆ | ario ´
quanto aos dados do mini-clima da estufa.
- | Sensor DHT11: O sensor DHT11 e respons ´ | avel por ´
realizar a mediçao de umidade relativa do ar (usando ˜ um sensor do tipo HR202 (entre 20% e 90%)) e da temperatura (usando um termistor NTC (entre 0 e 50 ◦C)). Possui quatro pinos: Vcc, GND, Dados (comunicaçao UART) e N.C (pino vazio). Possui uma ˜ biblioteca propria no Arduino #include¡dht.h¿. ´
Para escrever os dados no display, e necess ´ | ario separar ´
os dígitos. Por se tratar de um sensor de comunicaçaõ UART, e necessrio um delay entre uma leitura e a ´
outra. O MSP430 enviara um sinal para o ´ | slave (o
sensor) avisando que esta em modo de leitura e o ´
DHT11 enviara outro sinal para o ´ | master (o MSP430)
indicando que esta enviando dados. Ser ´ | a utilizada uma ´
interrupçao com o timer A para realizar o delay de ˜ leitura dos dados.
Possui uma biblioteca para MSP430 disponível no link do github a seguir: https://github.com/bafeigum/DHT11-Library-for-MSP430.
O princípio de funcionamento desta biblioteca é semelhante ao descrito anteriormente. E utilizado um ´
timer (o timer A) e uma interrupçao para comunicaç ˜ | aõ
com a placa:
- Precisa estar setado em UP mode e contando a cada 250 kHz (pode-se utilizar o SMCLOCK sendo /4);
- ISR seta um volatile unsigned char TOUT no
TA0. Esse ISR tambem dever ´ | a dar clear na ´
interrupt flag, setando CCIFG no registrador TACCL0;
- Sao enviados 5 elementos de um vetor ˜ (chamado packet) para o MSP430: packet[0] = primeiro byte de umidade packet[1] = segundo byte de umidade (deve ser ZERO)
packet[2] = primeiro byte de temperatura packet[3] = segundo byte de temperatura (deve ser ZERO)
packet[4] = byte da soma dos 4 bytes anteriores (usado para checagem dos dados (em caso de falha na comunicaçao)) ˜

Para melhor ilustrar o sistema, foi construído um Diagrama Logico que encontra-se nos anexos deste trabalho. ´

VI. REQUISITOS

- Uso do launchpad MSP430;
- | Controle do fluxo de agua com Rel ´ | es e v ´ | alvulas ´
| solenoides; ´
- Sensores de umidade e temperatura;
- Display para apresentaçao dos dados; ˜
- Fontes para fornecimento de 3.3 V, 5 V e 12 V para
| o sistema;

VII. BENEFÍCIOS

- | Uso da opçaõ | low-power mode do MSP430 pode
oferecer vantagem nos momentos em que nao estiver ˜ sendo utilizado;
- | Os reles e v ´ | alvulas todas e modo normalmente fechado ´
prove economia substancial de energia; ˆ
- Controle do consumo de recursos hídricos;
- Monitoramento do crescimento da planta e dos relacionados ao microclima no qual ela se encontra;
- Certeza de colheita no período de safra e entressafra;
- Economia de tempo e dinheiro para o produtor com o trabalho relacionado ao plantio e colheita dos morangos.

AGRADECIMENTOS

Os autores gostariam de agradecer aos colegas:

Arthur Wernke, Graduando em engenharia aeroespacial pela UnB - FGA; pelo auxílio no uso do compilador LATEXe
pela assistencia nos c ˆ | alculos de transporte de calor. ´
Victor Ribeiro Menezes, Graduando em engenharia aeroespacial pela UnB - FGA; pelo auxílio nos CAD’s da estrutura.

REFERENCES

[1] H. Kopka and P. W. Daly, A Guide to LATEX, 3rd ed. Harlow, England: Addison-Wesley, 1999.
[2] ROMANINI, Carlos E. B. et al

. Desenvolvimento e simulao de um sistema avanado de controle ambiental em cultivo protegido. Rev. Bras. Eng. Agrc. Ambient., [s.l.], v. 14, n. 11, p.1194-1201, 2010. FapUNIFESP (SciELO).
[3] RURALNEWS, Redao. Estufas - produo agrcola em ambientes controlados.2015.
Disponvel em: http://www.ruralnews.com.br/visualiza.php?id=202.
[4] ARAGUAIA, Mariana. Morango; Brasil Escola.
Disponvel em:

hhttp://brasilescola.uol.com.br/frutas/morango.htm. Acesso em 31 de setembro de 2017.
[5] PALHA, Maria da Graa. Manual do Morangueiro; 2005.
[6] Morato, J., Cruz, S., Pereira, .F, Metrlho, J. C.. Multi-Monitorizao de Estufas Agrcolas. Escola Superior de Tecnologia. Escola Superior Agrria. Instituto Politcnico de Castelo Branco.
[7] SOUSA, Andr Luiz C. N. D. e BUSSON, Bruna O.. Projeto de Sistema de Irrigao para Unidade de Agricultura Familiar. 2016.
[8] SCARPARE, Joo Alexio Filho. Vernalizao em cinco cultivares de morangueiro. 2007.
[9] HENZ, Gilmar P.; Desafios enfrentados por agricultores familiares na produo de morango no Distrito Federal. 2010.

ANEXOS


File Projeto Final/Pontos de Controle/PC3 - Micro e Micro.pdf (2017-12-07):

# Estufa Agrícola Automatizada com Auxílio do MSP430 para Cultivo de Morangos

Arthur Evangelista dos Santos Universidade de Brasília, Faculdade do Gama — UnB, FGA Matrícula: 14/0016686
Email: arthuevangelista@hotmail.com

Gabriela Conceiçao dos Santos ˜ Universidade de Brasília, Faculdade do Gama — UnB, FGA Matrícula: 16/0152038
Email: gabrielacsantos.engunb@gmail.com

Abstract—Este projeto visa criar um prototipo de estufa ´ agrícola automatizada para o cultivo de morangos aplicando
sensores eletronicos para controlar as condiç ˆ | oes de umidade e ˜
temperatura com auxílio do microcontrolador MSP430.

Keywords—MSP430, microcontrolador, automaçao, morangos, ˜ estufa.

I. REVISAÕ BIBLIOGRAFICA ´
A. O Morangueiro

O morangueiro pertence a Família Rosaceae. De origem Europeia, as plantas cultivadas para o consumo de sua fruta ´ sao o resultado de um sucessivo trabalho de melhoramento ˜
genetico e cruzamento entre algumas esp ´ | ecies do G ´ | enero ˆ
Fragaria. Atualmente, existem mais de 15 variedades de morangueiros. E um vegetal rasteiro, de caule do tipo estolho, ´ produzindo gemas que permitem com que novas plantas, com raízes e folhas, sejam formadas, assexuadamente. Uma imagem do morangueiro encontra-se abaixo na Fig. 1. No Brasil, sua produçaõ e mais significativa nos meses de junho a dezembro ´
e requer boa umidificaçao do solo. Por este motivo, ˜ | acaros e ´
pulgoes s ˜ | ao suas principais pragas. ˜


Fig. 1. Morangueiro

Desta planta origina-se o morango (Fig. 2), cuja parte
vermelha, comestível, e, na verdade, o recept ´ | aculo floral de- ´
senvolvido. Assim, ele e um pseudofruto; sendo os frutos, do ´ tipo aquenio, as estruturas amarronzadas que se encontram ˆ incrustadas nele.

Características gerais do cultivo do morango
:


Fig. 2. Fruto e pseudofruto do morango

- Clima: Locais com temperatura alta durante o dia e baixa durante a noite sao considerados bons para o ˜ cultivo do morangueiro. O calor e importante para o ´ crescimento vegetativo das plantas, enquanto o frio é
imprescindível a frutificaçao. A floraç ˜ | | aõ e favorecida ´
por temperaturas abaixo de 10 ◦C e desfavorecida por temperaturas acima de 25 ◦C. O comprimento do
dia, ou seja, o numero de horas de luz, tamb ´ | | | em tem ´
influencia sobre a produç ˆ | ao. A estas caracter ˜ | ísticas é
dado o nome de fotoperíodo.
Fotoperíodo trata-se da proporçao entre luz e es- ˜ curidao num ciclo de 24 horas (Santos, D.M.M., ˜ 2004). O morango, classificado como planta C3
quanto a fotoss ` | íntese e short-day plant (SDP) quanto
ao fotoperíodo, deve estar exposto por volta de 8 a 10
horas de luz diaria. O per ´ | íodo de escuridao tamb ˜ | em´
possui influencia na produç ˆ | ao de flores. Por ˜ | em, o ´
pouco excesso de iluminaçao devido ˜ | as condiç ` | oes ˜
de solstício ou equinocio na regi ´ | ao n ˜ | ao ter ˜ | a tanta ´
influencia no desenvolvimento do vegetal. Por este
motivo, nao optou-se por um pl ˜ | astico preto ou de ´
coloraçao que evitasse a exposiç ˜ | aõ a iluminaç ` | | ao. ˜
Para manter o fotoperíodo em condiçoes ideias de ˜
plantio, sera utilizada uma interrupç ´ | ao no MSP430 que ˜
ativara um LED capaz de fornecer o espectro de luz ´ apropriado para a planta.
- Sistemas de cultivo: O morango pode ser cultivado em
canteiros a ceu aberto, em estufas e em combinaç ´ | aõ
com o uso de tunel baixo. Atualmente est ´ | | | a sendo ´
implantado o sistema de cultivo hidroponico. ˆ

- Local de plantio: O morangueiro produz melhor em solos areno-argilosos e bem drenados. As areas devem ´
ser de facil acesso e ter bom suprimento de ´ | agua ´
para irrigaçao. Deve ser evitado o plantio em local ˜ recentemente cultivado com tomate, batata, fumo ou
com o proprio morango. H ´ | a de se pesquisar sobre ´
outros metodos que tornem poss ´ | ível o plantio de
culturas morangos no mesmo local. Tambem deve ser ´ evitado o plantio em terras de baixa umida. ´
- Período de plantio: A epoca de plantio varia de acordo ´
com a regiao e a cultivaç ˜ | ao a ser plantada. De um ˜
modo geral, planta-se de janeiro a maio. Em regioes ˜
mais quentes, a epoca recomendada ´ | e de abril a ´
maio. Em locais com altitude acima de 1.000 metros, as cultivares de dia neutro podem ser plantadas até setembro.
- | Irrigaçao: A irrigaç ˜ | ao do morangueiro pode ser feita ˜
por aspersao, por ˜ | em o gotejamento (fertirrigaç ´ | ao) tem ˜
sido mais eficiente e economico. Por este motivo, ˆ
neste trabalho sera utilizado o m ´ | etodo de irrigaç ´ | aõ
por gotejamento. Geralmente irriga-se tres vezes por ˆ semana e com duraçao de 30 a 45 minutos, evitando ˜ o excesso de agua. ´
B. O Morangueiro no Distrito Federal

A cultura do morangueiro iniciou-se no Distrito Federal em meados da decada de 70, tendo sido primeiramente introduzida ´ e conduzida de forma empírica pelos agricultores de origem
japonesa vindos da regiao de Atibaia, S ˜ | ao Paulo, at ˜ | e hoje o ´
principal polo de produç ´ | ao de morango naquele estado. ˜

Estes agricultores pioneiros vieram iniciar o cultivo de hortaliças e de frutas para abastecer o novo mercado do Planalto Central. Muitos foram assentados pelo Instituto
Nacional de Colonizaçao e Reforma Agr ˜ | aria - INCRA, a partir ´
de 1970, no ”Projeto Integrado de Colonizaçao Alexandre ˜
Gusmao (PICAG)”, na Regi ˜ | ao Administrativa de Brazl ˜ | andia, ˆ
atualmente o principal produtor de morango do Distrito Federal.

A cultura do morango adaptou-se muito bem as condiçoes ˜ climaticas e de solo do Planalto Central, que apresenta altitude ´
de aproximadamente 1000 metros. Alem disso, essa regi ´ | aõ
possui temperaturas mais altas no verao, que favorecem a ˜
produçao de mudas e na sequ ˜ | encia passa por um inverno ˆ
ameno e seco, o que auxilia no período de floraçao, frutificaç ˜ | aõ
e melhora de forma significativa a qualidade dos frutos cultivados.
Segundo a Emater-DF (Empresa de Assistencia T ˆ | ecnica ´
e Extensao Rural do Distrito Federal), no ano de 2016, a ˜ safra de morangos no Distrito Federal alcançou cerca de 5250 toneladas, numeros que colocam o Distrito Federal na disputa ´ do sexto lugar da produçao nacional entre os estados produ- ˜
tores da fruta . Sao, em m ˜ | edia, 240 produtores de morango ´
em todo o DF. Desses, 35% de produtores agrícolas da cidade sao os que distribuem o que se consome no DF. ˜
C. Estufas Agrícolas

Em grande parte da historia da humanidade, fomos ´ caçadores-coletores. Ha cerca de 10.000 anos, começamos a ´ domesticar plantas e animais como uma forma de tornar a nossa oferta de alimentos mais acessível e previsível.

Sendo assim, para melhorar a produçao agr ˜ ícola, surgiram as estufas agrícolas. O objetivo do cultivo agrícola em estufas
e proporcionar um ambiente controlado, em relaç ´ | ao a fatores ˜
climaticos como temperatura, umidade, luz e quantidade de ´ agua (rega), para que as plantas possam ter um crescimento ´ em um ambiente ideal (Silva, 1976).

A estrutura de uma estufa agrícola depende bastante de
sua finalidade. Geralmente, e constitu ´ | ída por uma armaçao, ˜
de alumínio ou outro material resistente, com uma altura suficiente para poder cultivar e caminhar dentro sem incomodos, ˆ
ela e coberta por um pl ´ | astico transparente, em alguns casos ´
possui uma tela, conhecida como sombrite, que auxilia na regulagem da temperatura interna da estufa alem de ventiladores ´ e em alguns casos lampadas para o controle de luminosidade ˆ (Fig. 3).


Fig. 3. Estrutura de uma estufa convencional para o cultivo de morangos

O aumento significativo da utilizaçao de estufas se deu, ˜
em parte, pela criaçao do pl ˜ | astico, devido ao seu baixo custo e ´
versatilidade, porem existem outros fatores que influenciam tal ´ fato, como o melhor desenvolvimento do plantio, aumento de produtividade, colheita nas entressafras e produtos de melhor qualidade.
D. Automaçao de Estufas ˜

Em uma estufa existem diversas variaveis que podem ser ´ monitoradas e verificadas para o controle do plantio, como temperatura, umidade e luminosidade. Considerando o ponto de vista dos produtores agrícolas, a correta leitura dos dados e posterior tomada de decisao pode trazer resultados satis- ˜ fatorios. ´

A automatizaço de uma estufa ˜ | e uma excelente ferramenta ´
de auxílio ao agricultor, pois permite a tomada de deciso no ˜
momento certo, conforme a analise das vari ´ | aveis verificadas. ´

II. JUSTIFICATIVA

Apesar de ser considerado um dos maiores produtores de morango do Brasil, durante o de 2017, o Distrito Federal veio enfrentando um grave crise hídrica, o que afetou de

forma significativa a produçao de morangos nessa regi ˜ | ao. ˜
Segundo dados da Emater, a restriçao no abastecimento de ˜
agua provocou a diminuiç ´ | ao da ˜ | area plantada em cerca de ´
30%, de 150 hectares em 2016 para 105 hectares neste ano.
Alem disso, a desaceleraç ´ | ao na produç ˜ | ao de mercado de ˜
morangos do DF ocasionou a diminuiçao do n ˜ | umero de tra- ´
balhadores envolvidos direta e indiretamente com a atividade, gerando a queda na renda das famílias e do Produto Interno Bruto(PIB) do Morango.

Diante disso, a escolha do projeto de construçao de uma ˜ estufa automatizada foi motivada pela simples possibilidade de se oferecer uma nova alternativa para o melhoramento do cultivo de morangos no Distrito Federal , uma vez que a estufa proposta sera capaz de controlar todas as necessi- ´ dades da cultura e o ambiente da estufa, o que proporcionará aos produtores mais qualidade em seus frutos e uma maior
renda. Tambem ser ´ | a poss ´ | ível controlar a quantidade de agua ´
utilizada na irrigaçao da plantaç ˜ | ao gerando, consequentemente, ˜
economia de recursos hídricos e financeiros na produçao de ˜ morangos.

III. OBJETIVOS

Considerando que cada especie de planta necessita de ´
situaçoes clim ˜ | aticas diferentes e espec ´ | íficas para se desen-
volver, o projeto proposto tem o intuito de otimizar o cultivo de morangos atraves do desenvolvimento de uma estufa capaz de ´ gerenciar (monitorar e atuar) o controle das condiçoes ambien- ˜
tais dentro do ambiente da estufa atraves da disponibilizaç ´ | aõ
de recursos de automaçao como irrigaç ˜ | ao autom ˜ | atica, sistemas ´
de ventilaçao, iluminaç ˜ | ao e controle de temperatura ambiente, ˜
utilizando o microcontrolador MSP430.

Em resumo, os objetivos deste trabalho sao: ˜

- | Economia de agua devido a automaç ´ | ao do ambiente; ˜
- Captaçao de dados de umidade e temperatura ambi- ˜ ente;
- Captaçao de dados de umidade do solo; ˜
- Controle de irrigaçao da estufa; ˜
- | Controle da iluminaçao e do fotoper ˜ | íodo da planta;
- Controle da temperatura no ambiente interno da estufa;
- Apresentaçao dos dados adquiridos pelos sensores ao ˜ usuario. ´

IV. ESTRUTURA

A estrutura do prototipo da estufa foi inicialmente cons- ´ truída com canos PVC (Policloreto de Vinila) de 25 mm de
diametro, e coberta com filme pl ˆ | astico transparente. A escolha ´
desses materiais foi feita pois se tratam de materiais resistentes, acessíveis, de baixo custo e suprem bem as necessidades de controle do mini-ecossistema da estufa. Como mencionado
tambem na seç ´ | ao I-A, n ˜ | ao optou-se por um pl ˜ | astico preto ou ´
de coloraçao que evitasse a exposiç ˜ | aõ a iluminaç ` | ao. ˜

As dimensoes da estruturas foram determinadas a partir da ˜ densidade de plantio estipulada para o cultivo do morangueiro em estufas, onde esta define que o espaçamento entre os morangueiros deve ser de no mínimo 20 cm e altura maxima ´ que a planta pode atingir 30 cm.


Fig. 4. Vista Isometrica do CAD da Estrutura realizado no software CATIA. ´

V. COMPARTIMENTO PARA ELETRONICA ˆ

Tendo em vista a acomodaçao dos componentes ˜ eletronicos, optou-se por montar uma segunda estrutura ˆ para concentrar tais componentes. Trata-se de uma caixa de
madeira MDF onde serao concentrados: o MSP430, o m ˜ | odulo ´
level-shifter, o display de cristal líquido, a pastilha termica e ´
os coolers, as fontes de alimentaçao e o m ˜ | odulo rel ´ | e. Assim, ´
a realizaçao da manutenç ˜ | ao em algum destes componentes ˜
torna-se de facil acesso. Outra vantagem ´ | e a facilidade de ´
acesso quanto a etapa de testes nos componentes e validaçaõ de algoritmos no MSP430. Os demais componentes (os sensores DHT11, umidostato e o LED de espectro completo) devem interagir diretamente com o ambiente interno a estufa `
e, portanto, estao no interior do pl ˜ | astico transparente de ´
cobertura da estufa.
Esta caixa contara com aberturas para circulaç ´ | ao de ar na ˜
regiao inferior e na superior, como pode ser observado nas ˜ Fig. 6 e no detalhamento na Fig. 7. A motivaçao para esta ˜
configuraçao se d ˜ | a pela exaust ´ | ao do cooler de resfriamento ˜
da pastilha termica estar contida neste compartimento. A ´ configuraçao das aberturas inferiores favorece o estrangula- ˜ mento do fluxo de ar, aumentando sua velocidade e fazendo com que o ar frio e menos denso resfrie os componentes do compartimento interno. As aberturas superiores tambem´ estrangulam o fluxo de ar, fazendo com que o ar quente e interno do compartimento saia com maior velocidade para o ambiente externo.
Maiores detalhes quanto a configuraç ` | ao dos coolers e ˜
o funcionamento da pastilha termica estar ´ | ao na seç ˜ | ao VI. ˜


Fig. 5. Estrutura construída em cano PVC.

Resumidamente, a pastilha e um paralelep ´ | ípedo com pouca
espessura. Esta aquecera de um lado e resfriar ´ | a do outro ´
e as aletas de alumínio em conjunto com os coolers seraõ responsaveis pela troca de calor externo. Como ambos os lados ´ poderao aquecer ou resfriar, foram colocadas aletas e coolers ˜ nos dois lados. Este conjunto esta apoiado no compartimento ´
para eletronica e um dos lados estar ˆ | a virado para o interior da ´
estufa.

VI. VISAÕ GERAL DO SISTEMA

O sistema do projeto proposto pode ser dividido duas partes. Uma parte de hardware, dotado do microcontrolador
MSP430, sensores eletronicos, os quais s ˆ | ao encarregados pela ˜
aquisiçao de dados do sistema, e atuadores, respons ˜ | aveis por ´
irrigar, iluminar, ventilar e reduzir ou aumentar a temperatura. E uma parte de software, responsavel pelo processamento dos ´ dados e do controle dos perifericos atuadores. ´
A. Hardware
1) Lista de Componentes:
- MSP-EXP430G2553LP;
- Sensor de luz (LDR 5mm);
- Sensor de temperatura e umidade (DHT11);
- Resistores de 10kOhm;
- Transistor Mosfet BS170;
- Modulo sensor de umidade do solo (Umidostato); ´
- | Modulo rel ´ | e 4 canais; ´

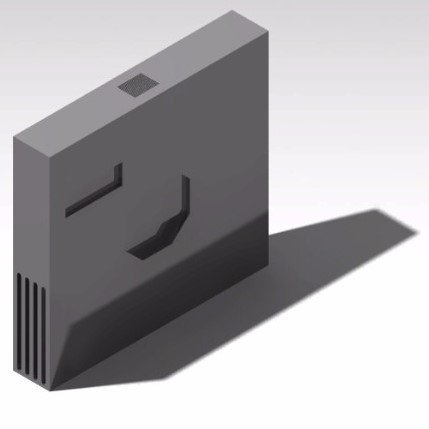
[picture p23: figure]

Fig. 6. Vista Isometrica do CAD do compartimento para eletr ´ | onica realizado ˆ
no software CATIA.


Fig. 7. Detalhamento da abertura superior do compartimento para eletronica. ˆ

- LED de espectro completo;
- Pastilha termina de efeito Peltier TEC1-12706; ´
- 2 Coolers de 12V;
- Fontes de 3,3V, 5V e 12V;
- | Valvula Solen ´ | oide. ´
2) Descriçao do Hardware: ˜ | Para melhor ilustrar a mon-
tagem dos componentes, foi realizado um diagrama de blocos para o sistema, que pode ser visualizado na Fig. 8. Uma breve
descriçao de cada componente ser ˜ | a apresentada a seguir. ´


Fig. 8. Diagrama de Blocos do sistema da estufa.

- MSP-EXP430G2553LP: O MSP430 sera o micro- ´ controlador responsavel pelo processamento dos dados ´ e a tomada de decisao de acordo com os dados. ˜ Este componente recebera os dados de temperatura e ´ umidade relativa do ar no interior da estufa, os dados de umidade do solo e os dados de luminosidade e
tomara as decis ´ | oes melhor descritas na seç ˜ | ao VI-A3. ˜
- Sensor de luz (LDR 5mm): Apos consultoria a ´
colegas da area de fisiologia vegetal e devido ´ | as`
características fotoperiodicas do morango, foi optado ´ pelo uso de um sensor de luminosidade LDR (Light Dependent Resistor) para identificar a existencia ou ˆ
nao de luminosidade na regi ˜ | ao pr ˜ | oxima ´ | a planta. O `
sensor e basicamente um resistor que ao submetido ´ | à
luz, aumenta sua condutividade eletrica. ´
- | Level-shifter para reduçao de tens ˜ | ao: ˜ | Uma mon-
tagem utilizando dois resistores de 10k ohm e um transistor mosfet BS170. O level-shifter reduz a tensaõ para que seja possível conectar componentes que
utilizam diferentes tensoes como n ˜ | ível logico alto. Se ´
um sinal chega com 3,3 V o level-shifter subira esta ´
tensao para 5 V em sua sa ˜ | ída para que seja utilizado
por outro componente.
A recíproca e verdadeira. Portanto, se um sinal tiver ´ 5 V, a saída do level-shifter tera 3,3 V. Testes foram ´ realizados com este componente para verificar se ele
funciona e quais os níveis de tensao em sua sa ˜ | ída.
Houve tambem uma preocupaç ´ | ao quanto a frequ ˜ | encia ˆ
maxima de operaç ´ | ao, uma vez que este componente ˜
sera utilizado na sa ´ | ída de todos os sensores e nas
saídas do MSP430. Foi confirmada o nível de ruído apresentado na saída do level-shifter a partir de 5MHz, o que ratifica a informaçao fornecida pelo ˜ datasheet do componente transistor BS170.
O esquematico desta montagem encontra-se na Fig. 9 ´ abaixo.
Tambem foi realizada um esquem ´ | atico para todos ´
redutores de tensao que ser ˜ | ao utilizados no projeto e ˜
foi montada um layout para placa de circuito impresso (PCB do inglesˆ printed circuit board). O intuito de se utilizar uma PCB e facilitar a montagem do circuito e ´
evitar perdas de tensao, diminuindo o ru ˜ | ído devido as`

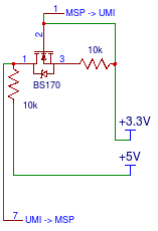
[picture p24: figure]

Fig. 9. Esquematico da unidade ´ | level-shifter (redutora de tensao). ˜
linhas de transmissao do sinal. At ˜ | e a data de redaç ´ | aõ
deste relatorio, a PCB encontra-se em sua vers ´ | ao 1.0. ˜
O estudo quanto ao uso de ground plate para reduçaõ
de ruído esta em andamento para as demais vers ´ | oes. ˜


Fig. 10. Esquematico do bloco de ´ | level-shifter’s utilizados no projeto.
- | Modulo rel ´ | e 4 canais: ´ | Sera utilizado um m ´ | odulo ´
com 4 reles para controle dos dispositivos com tens ´ | aõ
de 12V (pastilha termica e a v ´ | avula solen ´ | oide) e do ´
LED de espectro completo de 3,3V que consume uma corrente acima da suportada pelo MSP430
- Modulo sensor de umidade do solo (umidostato): ´ Possui formato de garfo (apenas duas pontas que
| deverao estar fincadas no solo). Ao identificar umidade ˜ ocorrera uma diferença de potencial entre as pontas do ´
garfo. A corrente que passara entre as duas pontas ´ | é
muito pequena (resistencia pr ˆ | oxima dos M ohm). ´
Quanto maior a resistencia, menor a umidade entre as ˆ ponteiras. A corrente, portanto, e muito baixa para que ´ se insira o sensor diretamente na porta analogica do ´

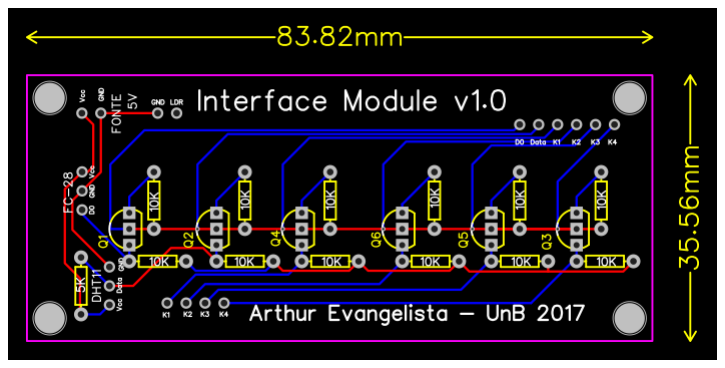
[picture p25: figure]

Fig. 11. Layout para PCB a ser confeccionada para o projeto.

micro. E necess ´ | ario o uso de um m ´ | odulo comparador. ´
Nada mais e que um amplificador operacional em ´ modo comparador. Quando comprado o sensor, o comparador LM393 (low offset voltage dual comparator) vem no conjunto.
A tensao de trabalho ˜ | e de 3,3 V a 5 V. O comparador ´
tem quatro pinos: Vcc, GND, D0 (digital) e A0
(analogico). Para usar a sa ´ | ída digital foi necessario ´
utilizar o potenciometro j ˆ | a encontrado no m ´ | odulo para ´
calibrar o sensor.
O potenciometro ir ˆ | a ajustar em qual medida de umi- ´
dade a saída digital tera n ´ ível logico zero. Podemos ´ utilizar uma entrada digital do MSP430 ativa em alta para identificar quando a umidade esta baixa. Ou seja, ´ Quando D0 = 1 a umidade esta baixa. Quando D0 = ´
0, ha umidade suficiente, n ´ | ao h ˜ | a necessidade de ligar ´
o irrigador (valvula solen ´ | oide). ´
Utilizaremos apenas o pino digital para o projeto. A leitura dos dados de umidade do solo podem ser comutados com a leitura dos dados de umidade do ar (DHT11), liberando a porta digital para outra aplicaçao. ˜
Utilizar uma porta analogica para leitura de dados ´ seria mais preciso, mas exigira um processamento do ´ sinal analogico antes deste ser inserido no microcon- ´ trolador (tecnicas de amostragem do sinal, uso do ´
criterio de Nyquist e o uso de uma m ´ | edia m ´ | ovel ou ´
filtro digital para evitar ruído ou sinais aleatorios ´ | ).
- Display de Cristal Líquido: Para visualizaço dos ˜ dados (umidade do ar, umidade do solo e temperatura) sera utilizado um display. Dependendo da temperatura ´ sera ativado um exaustor (ventilar a estufa) e uma ´ pastilha termica (aquece ou resfria o ambiente da est- ´
ufa). Da umidade do ar/solo serao ligadas as v ˜ | alvulas ´
de irrigaçao. ˜
Possui uma biblioteca na IDE do arduino: (#include¡LiquidCrystal.h¿) e pode ser facilmente implementada no MSP430 utilizando algoritmos disponíveis na documentaçao do fabricante. O display ˜
sera meramente utilizado para refer ´ | encia do usu ˆ | ario ´
quanto aos dados do mini-clima da estufa.
- | Sensor DHT11: O sensor DHT11 e respons ´ | avel por ´
realizar a mediçao de umidade relativa do ar (usando ˜ um sensor do tipo HR202 (entre 20% e 90%)) e da temperatura (usando um termistor NTC (entre 0 e 50 ◦C)). Possui quatro pinos: Vcc, GND, Dados

(comunicaçao UART) e N.C (pino vazio). Possui uma ˜ biblioteca propria no Arduino #include¡dht.h¿. ´
Para escrever os dados no display, e necess ´ | ario separar ´
os dígitos. Por se tratar de um sensor de comunicaçaõ
UART, e necess ´ | ario um delay entre uma leitura e a ´
outra. O MSP430 enviara um sinal para o ´ | slave (o
sensor) avisando que esta em modo de leitura e o ´
DHT11 enviara outro sinal para o ´ | master (o MSP430)
indicando que esta enviando dados. Ser ´ | a utilizada uma ´
interrupçao com o timer A para realizar o delay de ˜ leitura dos dados.
Possui uma biblioteca para MSP430 disponível no link do github a seguir: https://github.com/bafeigum/DHT11-Library-for-MSP430.
O princípio de funcionamento desta biblioteca é semelhante ao descrito anteriormente. E utilizado um ´
timer (o timer A) e uma interrupçao para comunicaç ˜ | aõ
com a placa:
- Precisa estar setado em UP mode e contando a cada 250 kHz (pode-se utilizar o SMCLOCK sendo /4);
- ISR seta um volatile unsigned char TOUT no
TA0. Esse ISR tambem dever ´ | a dar clear na ´
interrupt flag, setando CCIFG no registrador TACCL0;
- Sao enviados 5 elementos de um vetor ˜ (chamado packet) para o MSP430: packet[0] = primeiro byte de umidade packet[1] = segundo byte de umidade (deve ser ZERO)
packet[2] = primeiro byte de temperatura packet[3] = segundo byte de temperatura (deve ser ZERO)
packet[4] = byte da soma dos 4 bytes anteriores (usado para checagem dos dados (em caso de falha na comunicaçao)) ˜
- | Valvula Solen ´ | oide: ´
- LED de Espectro Completo: O LED de espectro completo utilizado pode ser visualizado na Fig. 12 abaixo. Este LED utiliza uma alimentaçao de 3,3V ˜ e consome por volta de 0,9 A de corrente, fornecendo quase 3W de potencia luminosa para o sistema. De ˆ
acordo com o grafico da Fig. 13, dispon ´ | ível no
datasheet do componente, o espectro de luz que este
LED fornece e o suficiente para manter a fotoss ´ | íntese
da planta no trecho de claridade de seu fotoperíodo. Para controlar este LED, sera utilizado o canal K1 do ´
rele, ligado a uma das sa ´ | ídas do MSP430. A escolha
para esta configuraçao se deve ˜ | a corrente consumida `
pelo LED que e muito superior ´ | a maior corrente `
fornecida pelo MSP430. Outra vantagem de se utilizar
o modulo rel ´ | é e a proteç ´ | ao contra fugas de corrente ˜
do rele para o dispositivo que o controla. ´
- Pastilha Termica de Efeito Peltier TEC1-12706: ´
Sera utilizada uma pastilha t ´ | ermica de efeito Peltier ´
(TEC1-12706) em conjunto com os Coolers de 12V para o aquecimento e resfriamento da estufa. Esta pastilha necessita de uma fonte de alimentaçao de ˜ 12V e consome ate 6A para manter o efeito em ´ sua superfície. O efeito Peltier ocorre quando dois


Fig. 12. LED de espectro completo e da PCB de alumínio do conjunto.


Fig. 13. Grafico da caracter ´ | ística optica do LED de espectro completo ( ´ | fonte:
3W High Power LED datasheet).
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

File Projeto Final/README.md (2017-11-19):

  # Projeto Final
  
  Pasta dedicada para o projeto final. Pontos de Controle, código, esquemático do projeto e afins estão contidos nesta pasta.
  Grupo:
    
    Nome: Arthur Evangelista dos Santos
    Matrícula: 14/0016686
    
    Nome: Gabriela dos Santos
    Matrícula: 16/0152038

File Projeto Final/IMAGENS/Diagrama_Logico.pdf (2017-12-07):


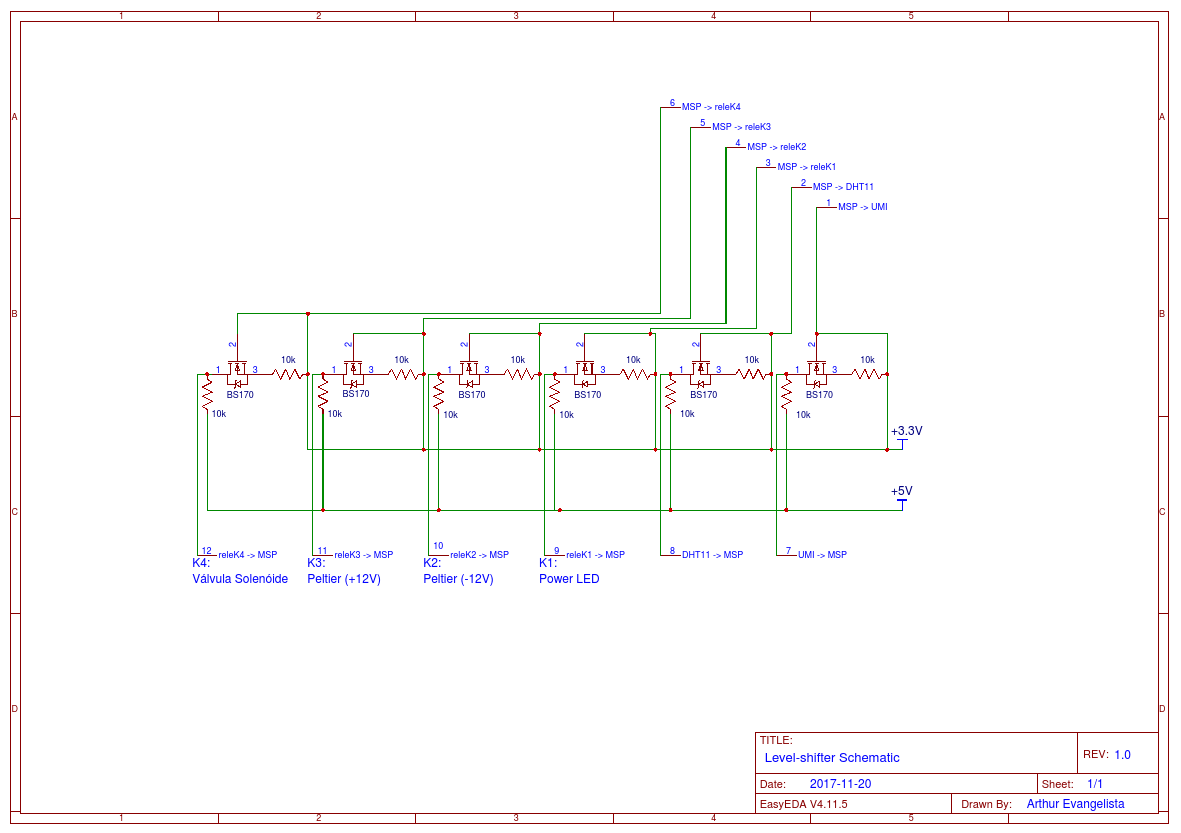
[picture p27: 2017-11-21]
Projeto Final/Level-Shifter-Schematic.png

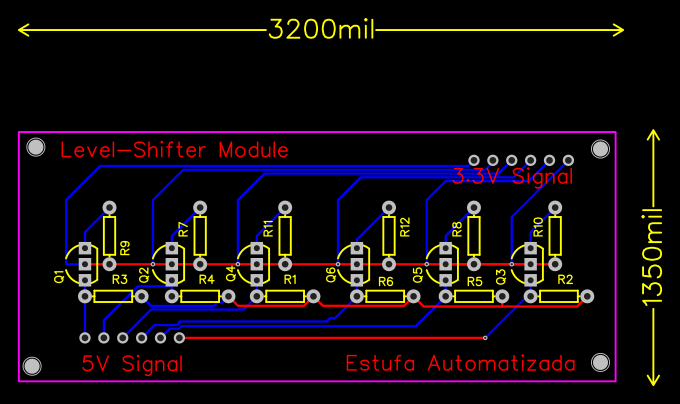
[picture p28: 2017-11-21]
Projeto Final/Level-Shifter-PCB.png

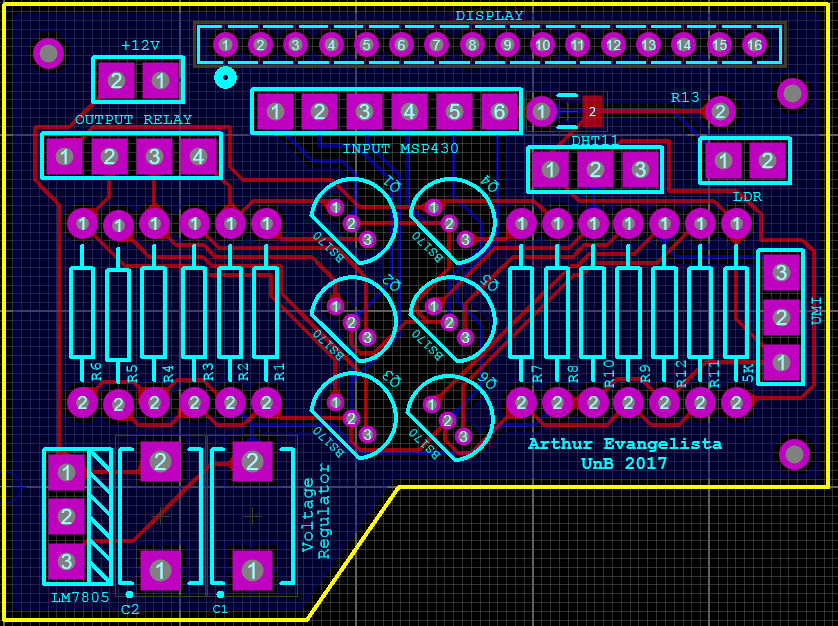
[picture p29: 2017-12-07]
Projeto Final/IMAGENS/Interface-PCBv3.png

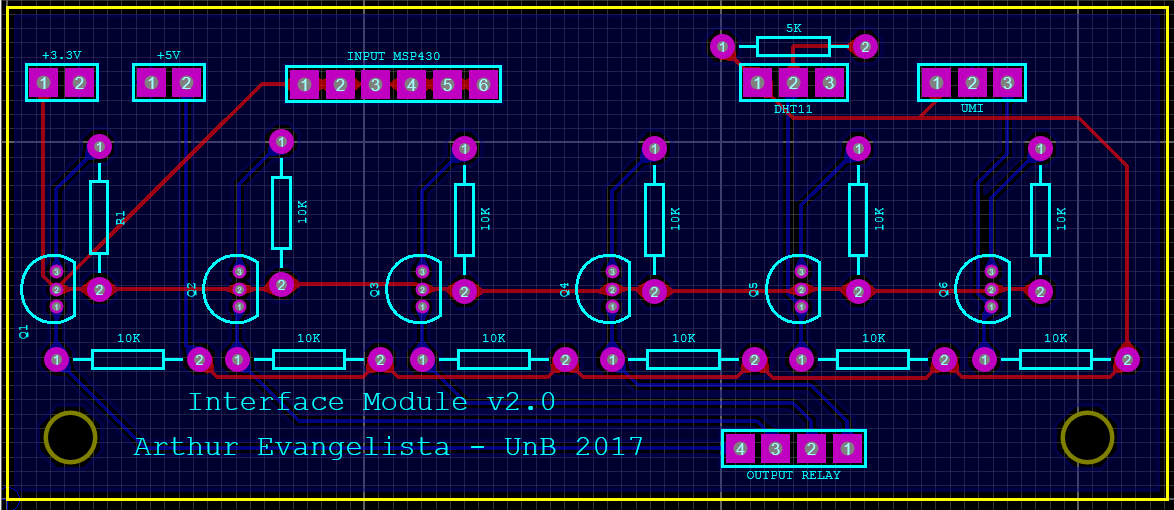
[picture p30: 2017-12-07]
Projeto Final/IMAGENS/Interface-PCBv2.png

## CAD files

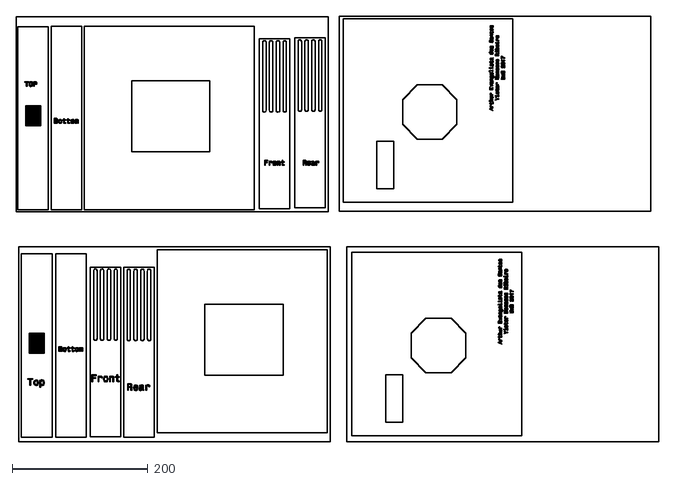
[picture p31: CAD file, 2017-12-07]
Projeto Final/DXF Files/Drawing3.dxf
945.1 x 626.1

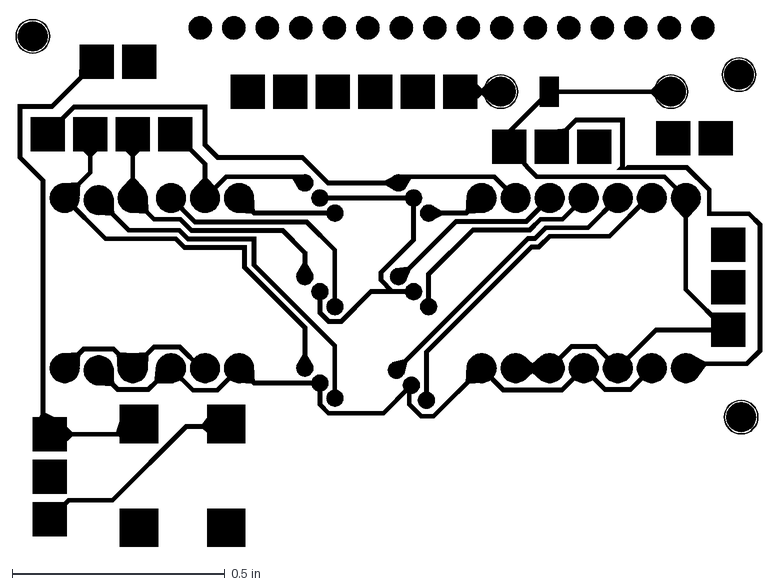
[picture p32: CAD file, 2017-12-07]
Projeto Final/DXF Files/Top Copper.dxf
1.75 x 1.25 in

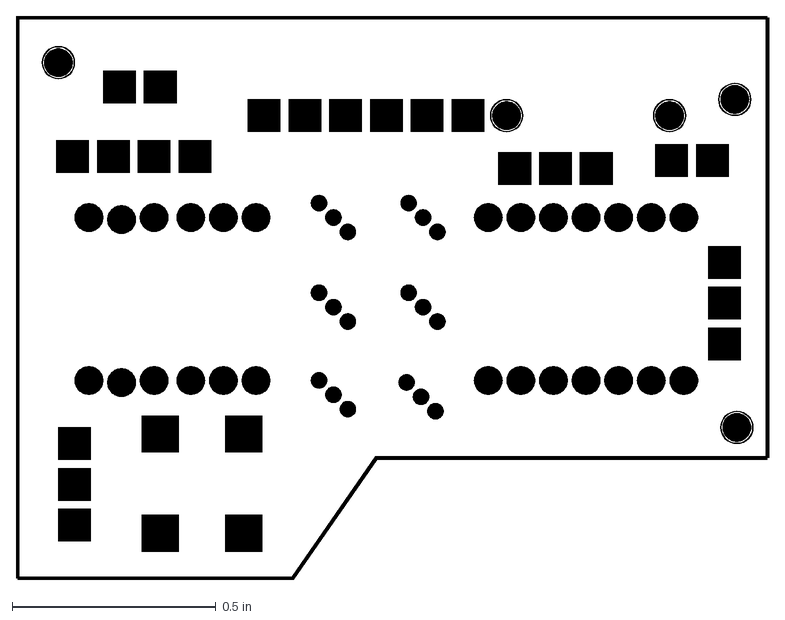
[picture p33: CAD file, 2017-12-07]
Projeto Final/DXF Files/Board Edge.dxf
1.85 x 1.38 in

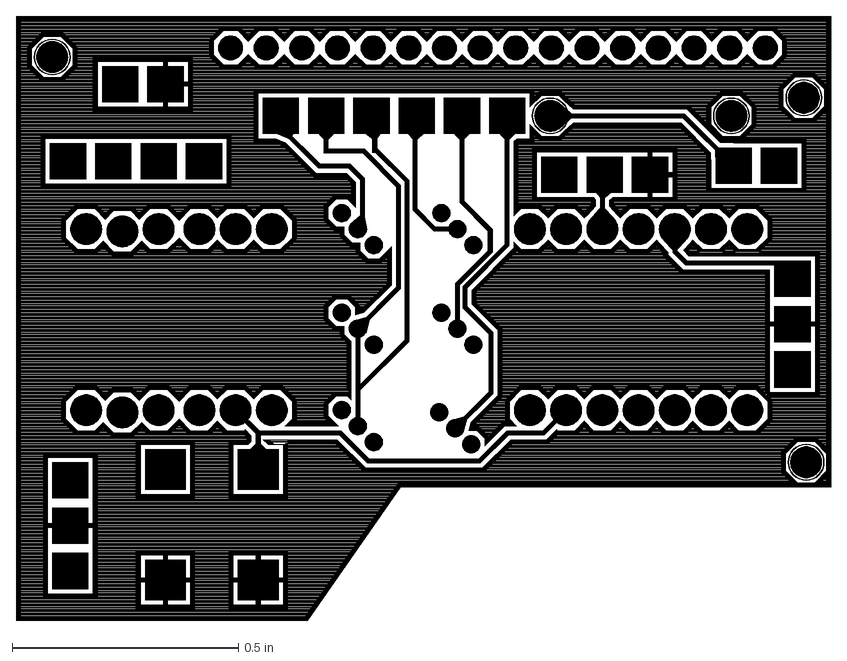
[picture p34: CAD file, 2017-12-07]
Projeto Final/DXF Files/Bottom Copper.dxf
1.80 x 1.33 in

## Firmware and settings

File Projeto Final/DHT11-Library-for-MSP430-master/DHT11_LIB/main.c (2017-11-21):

/*
 * 
 * Engineer: Bryce Feigum (bafeigum at gmail)
 * Date: December 22, 2012
 *
 * Version: 1.0 - Initial Release
 * Version: 1.1 - Added GNUv2 License
 *
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
 * You should have received a copy of the GNU General Public License
 * along with this program; if not, write to the Free Software
 * Foundation, Inc., 51 Franklin Street, Fifth Floor, Boston, MA  02110-1301, USA.
 * Project:	DHT11_LIB
 * File:	main.c
 */
#include <msp430.h>
#include <DHT11_LIB.h>

unsigned char RH_byte1;
unsigned char RH_byte2;
unsigned char T_byte1;
unsigned char T_byte2;
unsigned char checksum;

unsigned char Packet[5];

void init(void);

unsigned char volatile TOUT;			//REQUIRED for library
unsigned char volatile SECOND_TIMER=0;

#pragma vector = TIMER0_A0_VECTOR
__interrupt void CCR0_ISR(void){
		SECOND_TIMER++;
		TOUT=1;
		TOG (P1OUT,0x01);
		CLR (TACCTL0, CCIFG);
}

void main(void) {
	init();
	
	while(1){
		//Must wait 1 second initially and between all reads
		if(SECOND_TIMER >= 5){		//5 @ CCR0 = 50000 & div 4
			// Manual way to gather all data without array
			/*
			start_Signal();
			if(check_Response()){
				RH_byte1 = read_Byte();
				RH_byte2 = read_Byte();
				T_byte1 = read_Byte();
				T_byte2 = read_Byte();
				checksum = read_Byte();
			}
			*/

			//	Simple way to gather all data with one instruction
			read_Packet(Packet);
			RH_byte1 =	Packet[0];
			RH_byte2 =	Packet[1];
			T_byte1 =	Packet[2];
			T_byte2 =	Packet[3];
			checksum =	Packet[4];

			if (check_Checksum(Packet))
				SET (P1OUT, 0x40);

			SET (TACTL, TACLR);
			SET (TA0CTL, 0x10);
			TACCR0 = 50000;		//Initialize the timer to count at 5Hz
			SECOND_TIMER = 0;	//Clear counter
		}
	}
}

void init(){
	WDTCTL = WDTPW + WDTHOLD;	// Stop watchdog timer

	P1OUT  = 0x00;				//Start with nothing being output
	P1DIR  = 0x41;				// Set LED to output direction

	BCSCTL1 = CALBC1_1MHZ; 		// Set oscillator to 1MHz
	DCOCTL = CALDCO_1MHZ;  		// Set oscillator to 1MHz

	TACCR0 = 50000;				// Initialize the timer to count at 5Hz
	TACCTL0 = CCIE;				// Enable interrupt
	TA0CTL = TASSEL_2 + ID_2 + MC_1 + TACLR;	// SMCLK, div 4, up mode,
												// clear timer
	_enable_interrupt();						//Enable global interrupt
}

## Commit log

2017-08-18 Há observação
    Obs.: Não é possível realizar soma de um reg com ele mesmo?
2017-09-06 Update
    Buscar referência na linha 8;
    Buscar referências quanto a estatísticas úteis em uma estufa/lavoura na linha 14;
    Buscar referências sobre Relé e Válvula Solenóide;
    Pasta Pontos de Controle criada;
2017-10-04 Agora atualizou de verdade
2017-10-04 Agora atualizou de verdade verdadeira
2017-10-20 Atualizado com documentação do sensor DHT11
2017-12-07 Todos os arquivos adicionados pro github
    [Board Edge.dxf, Bottom Copper.dxf, Drawing3.dxf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]

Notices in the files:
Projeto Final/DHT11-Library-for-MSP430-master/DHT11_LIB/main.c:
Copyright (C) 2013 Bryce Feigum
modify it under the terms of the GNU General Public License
